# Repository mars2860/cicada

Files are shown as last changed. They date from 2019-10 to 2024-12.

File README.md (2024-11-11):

### About

The Cicada Project is the flight controller based on ESP8266 Wifi module. You can make it yourself to come in the world of drone developers. Cicada doesn't have a hardware pult with sticks. To control a drone there is desktop application developed on Java and mobile application for Android v7 and higher. You can connect a gamepad to your smartphone or desktop to control a drone. The flight controller can work in WiFi normal mode as WiFi station or WiFi Access Point. Also It can work in WiFi Broadcast mode (WiFi monitor mode). To work in broadcast mode you have to connect the special wifi broadcast serial modem to your smartphone or desktop. The serial modem is easy. You can do it yourself easy. Just ESP-07 module + UART-USB bridge. Flash in ESP-07 the modem firmware which is placed in the folder /firmware/WifiBroadcastModemFw.

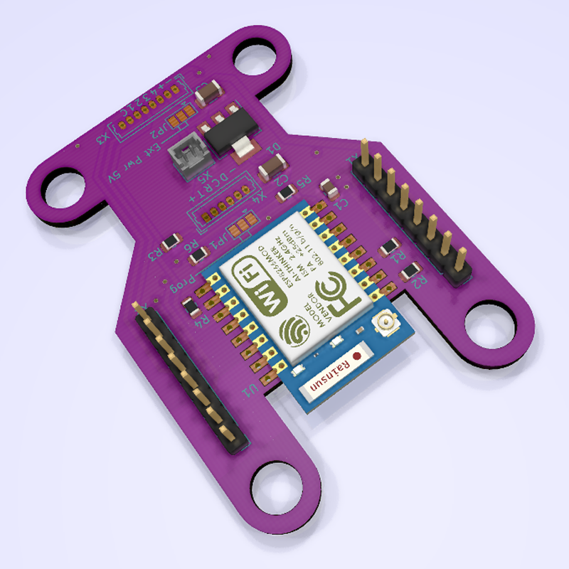
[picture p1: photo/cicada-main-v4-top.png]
cicada-main-v4

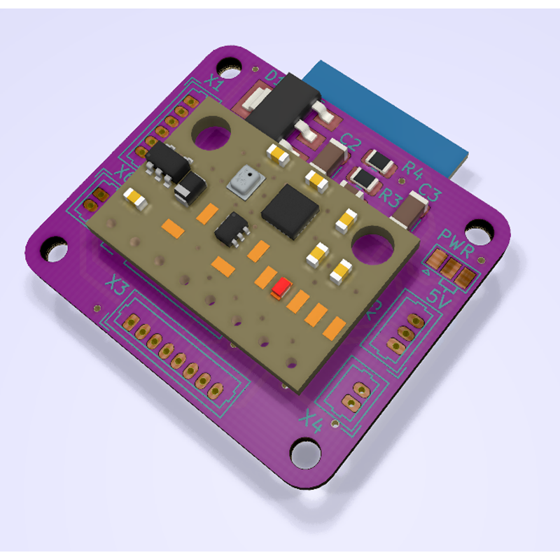
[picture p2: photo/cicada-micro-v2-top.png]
cicada-micro-v2

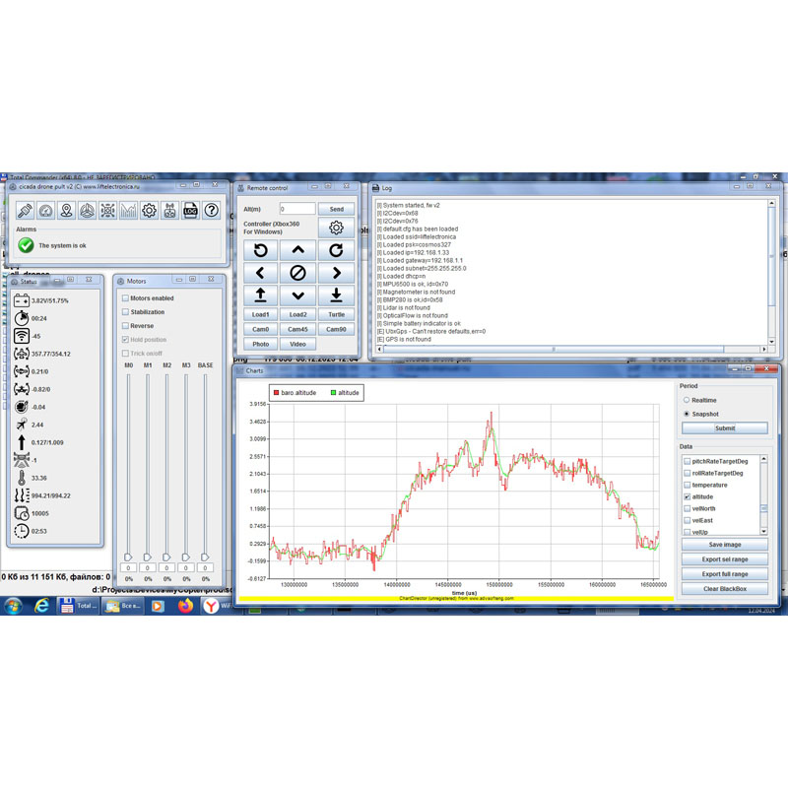
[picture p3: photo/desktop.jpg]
DesktopApp

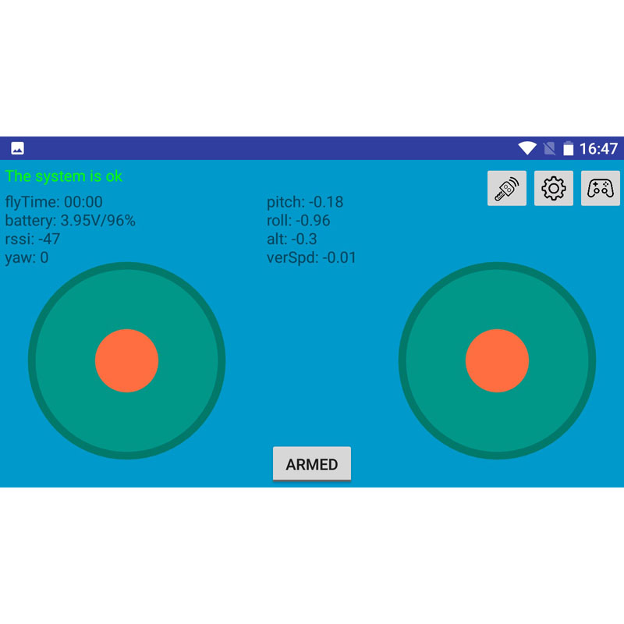
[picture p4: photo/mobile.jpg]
MobileApp


### Features

| | | | |
| --- | --- | --- | --- |
| | **Min** | **Typ** | **Max** |
| **1\. Supply voltage** | 3,4V | | 5V  |
| **2\. Update frequency** | | 100 Hz | |
| **3\. Control from notebook or smartphone through WiFi net.** | | 2.4 GHz | |
| **4\. Instant telemetry through WiFi net.** Charts of all parameters. BlackBox is stored on host. Telemetry packets is sent every 10ms. | | | |
| **5\. Control devices:**<br><br>* Gamepad (supported by desktop and mobile applications)<br>* Keyboard (supported by desktop application only)<br>* Virtual keyboard (supported by desktop application only)<br>* Virtual gamepad (supported by mobile application only) | | | |
| **6\. Control range** | | | 100 meters |
| **7\. Stabilization modes:**<br><br>* Stabilization of body angular rates<br>* Stabilization of yaw,pitch,roll angles<br>* Stabilization of vertical velocity (only if barometer or lidar are available in the system)<br>* Stabilization of horizontal velocity (only if optical flow sensor or GPS are available in the system) | | | |
| **8\. Supported sensors and devices:**<br><br>* MPU9250 - imu chip<br>* MPU6500 - imu chip<br>* MPU6050 - imu chip<br>* QMC5883L - magnetometer<br>* BMP280 - barometer<br>* VL53L1X - lidar<br>* TFmini Plus (in I2C mode) - lidar<br>* HCSR04 (in I2C mode) - sonar<br>* BN180 and other GPS modules with UBX protocol<br>* Analog 0-3V sensor of battery current<br>* Servo 500-2400us to control camera pitch angle<br>* Camera Runcam Split4 (only supported start/stop video commands) | | | |
| **9\. Electronic speed controllers:**<br><br>* DSHOT-300 to control BLDC motors<br>* All listed below PWM-modesе to direct control coreless dc motors<br>* PWM 2.5 kHz, resolution 2000<br>* PWM 5 kHz, resolution 1000<br>* PWM 10 kHz, resolution 500<br>* PWM 20 kHz, resolution 250<br>* PWM 40 kHz, resolution 125<br>* PWM 50 kHz, resolution 100 | | | |
| **10\. Dimensions**<br><br>* cicada-main-v4<br>* cicada-micro-v2 | | 58,67mm х 41,65mm  <br>26,67mm x 30,98mm | |
| **11\. Installation dimensions**<br><br>* cicada-main-v4<br>* cicada-micro-v2 | | 48,51mm х 31,49mm  <br>21,84mm x 26,16mm | |
| **12\. Weight**<br><br>* cicada-main-v4 with cicada-gy91-v3<br>* cicada-micro-v2 | | 16g  <br>6g | |
	
### Drones

Examples of drones you can find in drones folder of this project.

### Firmware

The firmware is based on PDL. Portable Drone Logic (PDL) is the lightweight pure C library implements a common drone logic. The goal of PDL is to be easy to use and easy to port to your hardware platform. PDL supports only quadcopters at this time.

It provides for you
- data model
- application template
- task scheduler
- chain of PIDs
- parser for binary digital commands

PDL is a part of this project. But you can use it to create firmware for your own hardware platform. Documentation is available in /firmware/CicadaFw/libraries/pdl

To build firmware you need
- Install Sloeber IDE https://github.com/Sloeber/arduino-eclipse-plugin/releases/
- Run Sloeber IDE. Go to Arduino->Preferences->Platforms and Boards. Download latest version of ESP8266 platform
- Install I2C driver https://github.com/enjoyneering/ESP8266-I2C-Driver
- Create ssid_config.h file with your wifi-net settings. For example

Firmware supports update by the air. It is based on ESP8266HTTPUpdateServer.

### Chain of PIDs

Chain of PIDs

### Design tools

- Sloeber IDE
- FreeCAD
- KiCAD

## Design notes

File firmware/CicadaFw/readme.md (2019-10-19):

### How to build

1. Install Sloeber IDE https://github.com/Sloeber/arduino-eclipse-plugin/releases/
2. Run Sloeber IDE. Go to Arduino->Preferences->Platforms and Boards. Download latest version of ESP8266 platform
3. Install I2C driver https://github.com/enjoyneering/ESP8266-I2C-Driver

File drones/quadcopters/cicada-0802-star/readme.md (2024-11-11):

# Cicada-0802

Cicada-0802-star is FPV quadcopter based on Cicada Flight Controller. Distance between motors 75mm in diagonal. Mass is 48 gram with GNB-380mAh-LiHv-1S. Time of flight is about 2 minutes.

# Parts List
- cicada-micro-v2 - flight controller based on ESP-12E module
- teeny pro 5a - electronic speed controller
- happymodel RS0802 KV20000 - motors
- HQProp 40MMX3GR  - propellers
- akk ba3 - camera

# Electrical schematic
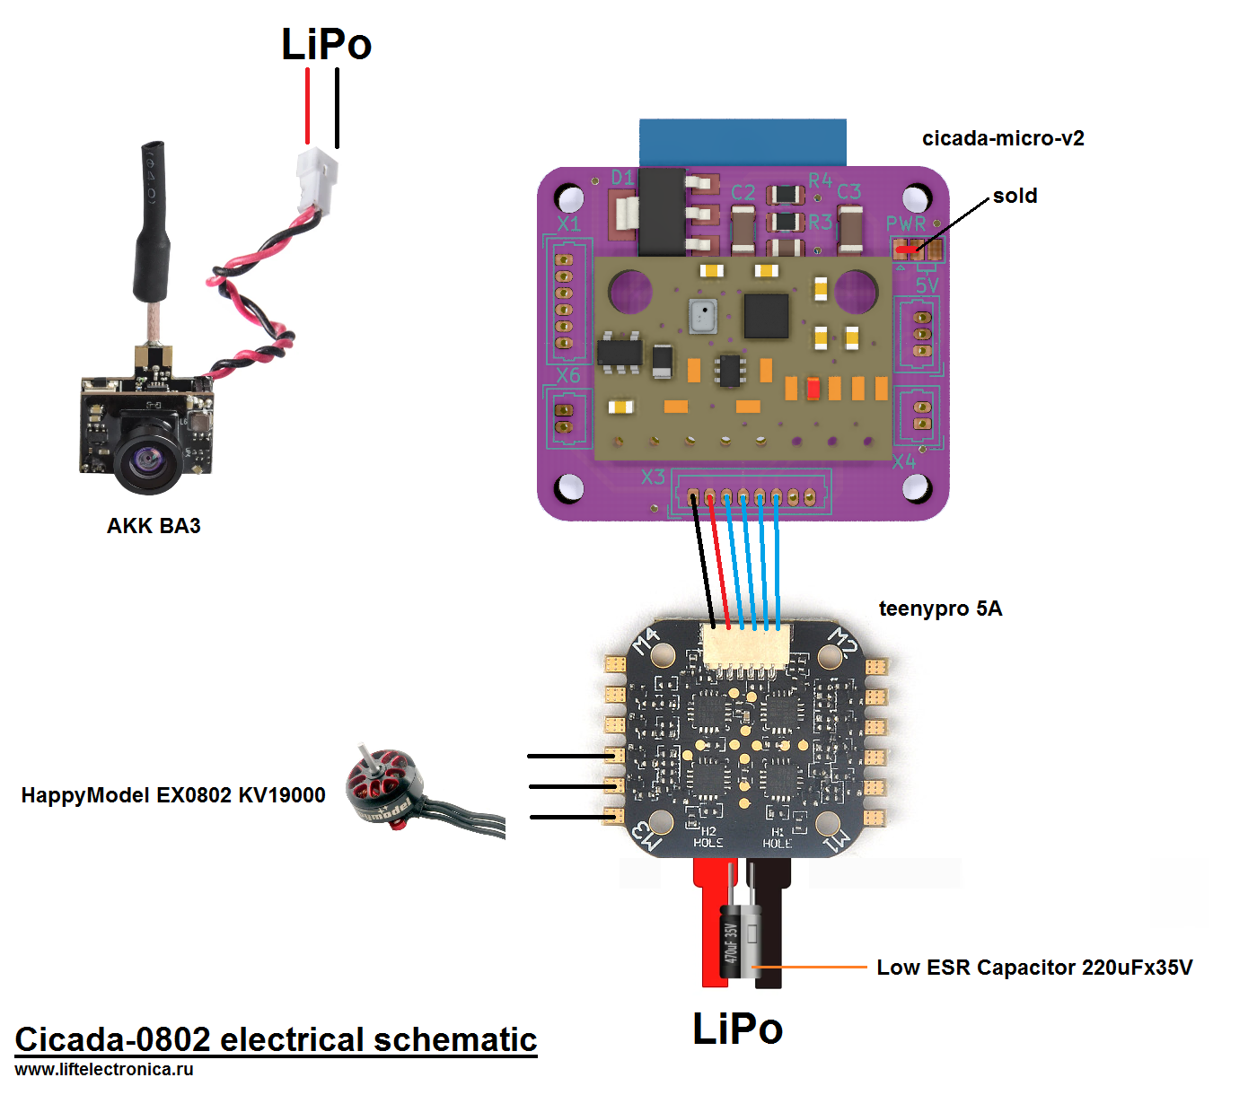
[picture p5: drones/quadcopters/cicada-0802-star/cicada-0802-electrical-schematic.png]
electrical schematic


# Views
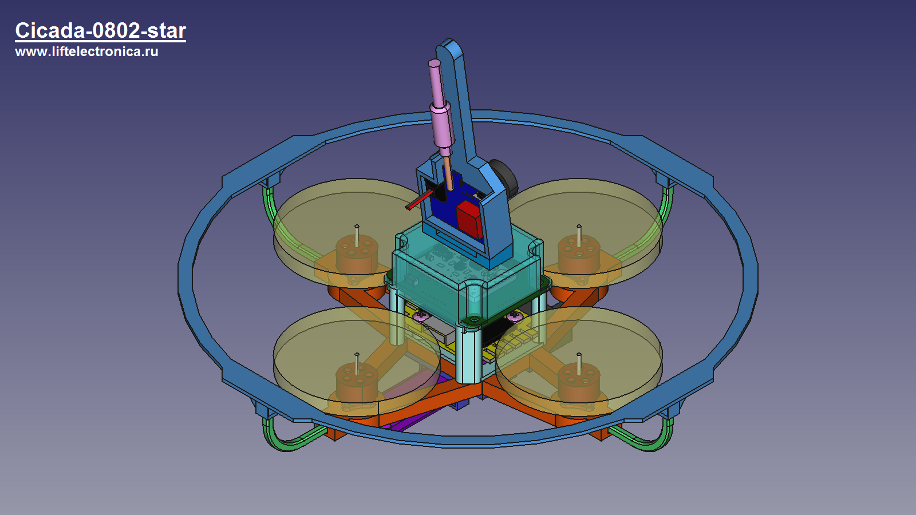
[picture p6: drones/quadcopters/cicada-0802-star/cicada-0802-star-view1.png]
view1

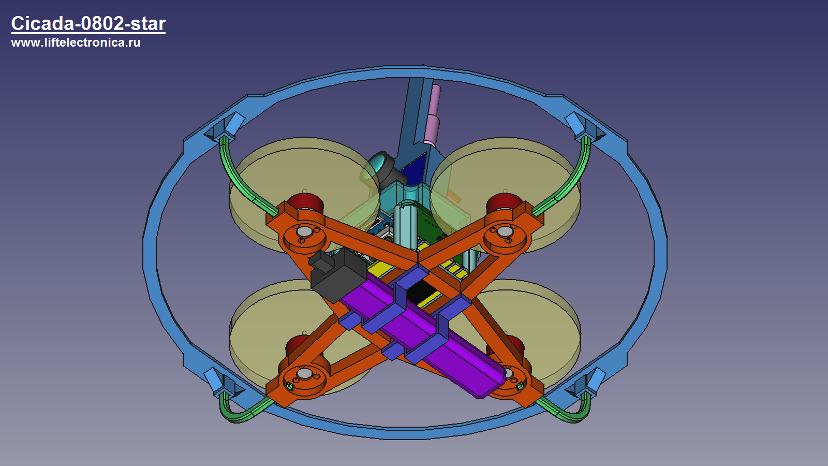
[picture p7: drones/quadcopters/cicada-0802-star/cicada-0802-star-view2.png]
view2


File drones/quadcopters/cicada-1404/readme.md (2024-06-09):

# Cicada-1404

Cicada-1404 is FPV quadcopter based on Cicada Flight Controller. Distance between motors 170mm in diagonal. Mass is 225 gram without gps module and propeller protection. As optional it can be equipped with GPS module. Time of flight is about 6 minutes with GNB-850mAh-80C-2S battery

# Parts List
- cicada-micro-v2 - flight controller based on ESP-07 module
  -- ESP-07 - wifi module (https://aliexpress.ru/item/32226333667.html)
  -- GY-91 module (https://aliexpress.ru/item/1005004770424192.html)
  -- LDL1117S33SR (https://www.chipdip.ru/product/ldl1117s33r-stm)
  -- Resistors 0805 3k3 6pieces (https://www.chipdip.ru/product0/8001961333)
  -- Resistor 0805 390k 1pieces (https://www.chipdip.ru/product0/8002001295)
  -- Resistor 0805 30k 1pieces (https://www.chipdip.ru/product0/8001968464)
  -- Capacitor 0805 100nF 1pieces (https://www.chipdip.ru/product/grm21br71h104k)
  -- Capacitor 1206 22uF 2pieces (https://www.chipdip.ru/product0/9001437124)
- skystars ko25 - electronic speed controller (https://aliexpress.ru/item/1005003703593525.html)
- skystars koko 1404 KV4600 - motors (https://aliexpress.ru/item/1005002967385400.html)
- HQProp T3x2x2 - propellers (https://aliexpress.ru/item/4000082192022.html)
- runcam split4 - camera (https://aliexpress.ru/item/4001286069840.html)
- akk fx3 - 5.8 GHz video transmitter (https://aliexpress.ru/item/32886948514.html)
- antenna 5.8 GHz with MMCX connector (https://aliexpress.ru/item/4000109363746.html)
- SG-90 - servo to control camera pitch (https://aliexpress.ru/item/1005006027280940.html)
- IFlight M8Q-5883 - GPS module (optional) (https://aliexpress.ru/item/1005006376325669.html)
- gnb-850-80C-2S - battery (https://aliexpress.ru/item/1005005952282974)
- mp1584en - dc-dc step down power module (https://aliexpress.ru/item/1005001621925314.html)

# Electrical schematic
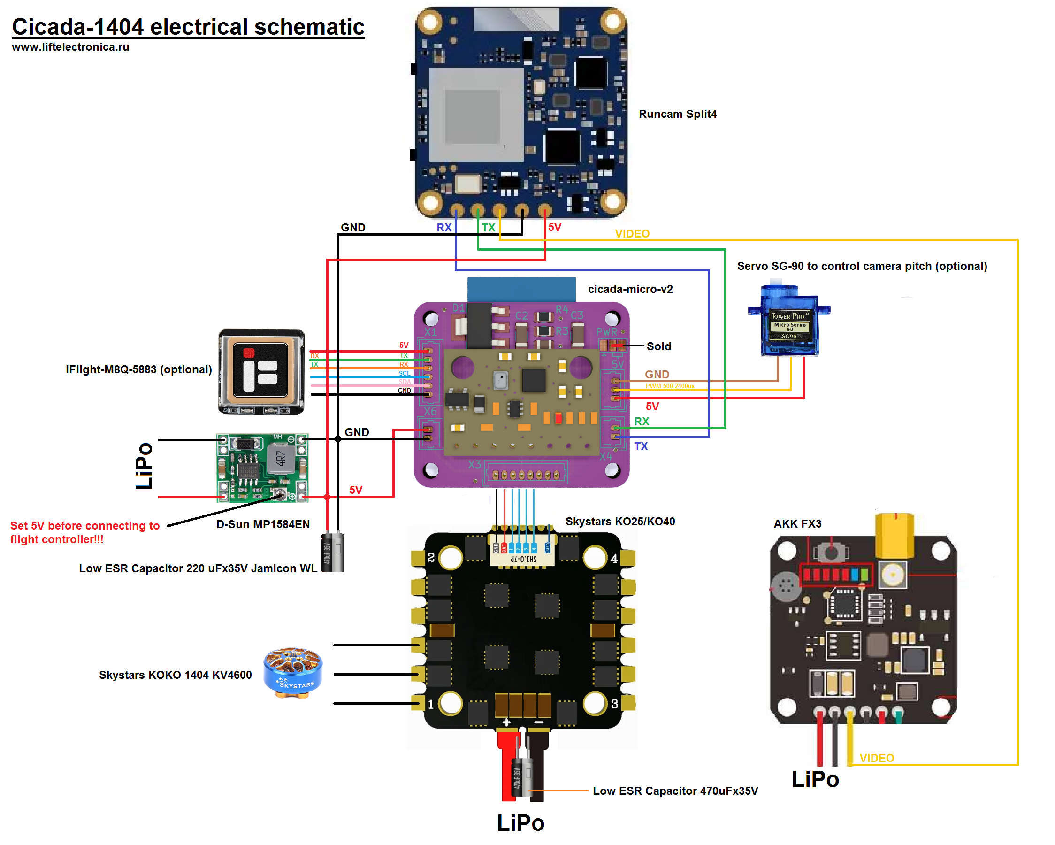
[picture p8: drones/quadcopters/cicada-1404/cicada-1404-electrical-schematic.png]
electrical schematic


# Views
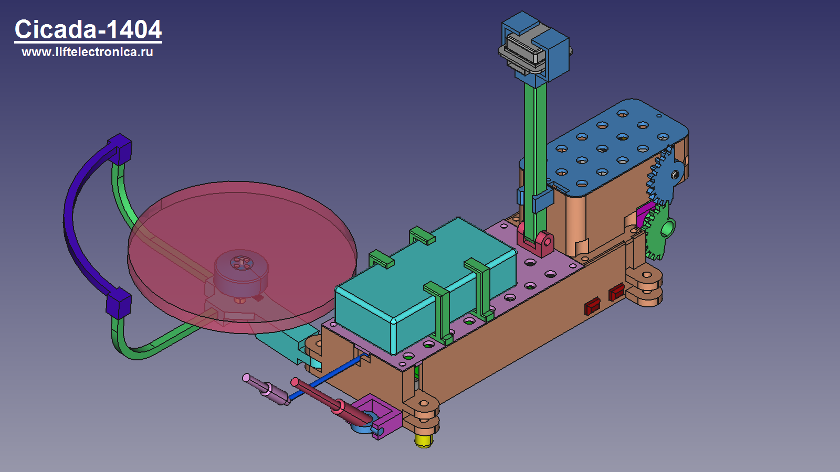
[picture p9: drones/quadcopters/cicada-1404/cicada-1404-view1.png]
view1

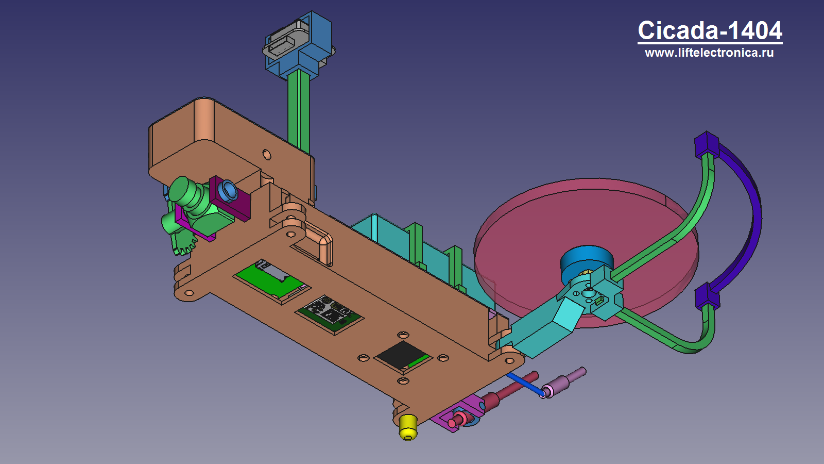
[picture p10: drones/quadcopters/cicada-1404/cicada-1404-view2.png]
view2


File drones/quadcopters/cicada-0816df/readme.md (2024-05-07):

# Cicada-0816df

Cicada-0816df is FPV quadcopter based on Cicada Flight Controller. Distance between motors 96mm in diagonal. Mass is 94 gram. Time of flight is about 2 minutes with GNB-550mAh-90C-1S battery. Ducted fans were made based on [this article](https://capolight.wordpress.com/2015/01/14/quadcopter-rotor-duct/) Its really increase thrust of propellers but this increasing is eaten by weight of ducts. Also ducted fans increase stabilization by pitch/roll but strongly decrease stabilization by yaw.

# Parts List
- cicada-micro-v2 - flight controller based on ESP-12E module
- cicada-pwm-esc-v3 - electronic speed controller
- coreless dc 816 motors
- HQProp 41mm-3blades or Gemfan 1636 - propellers
- ewrf7082ve - camera

# Electrical schematic
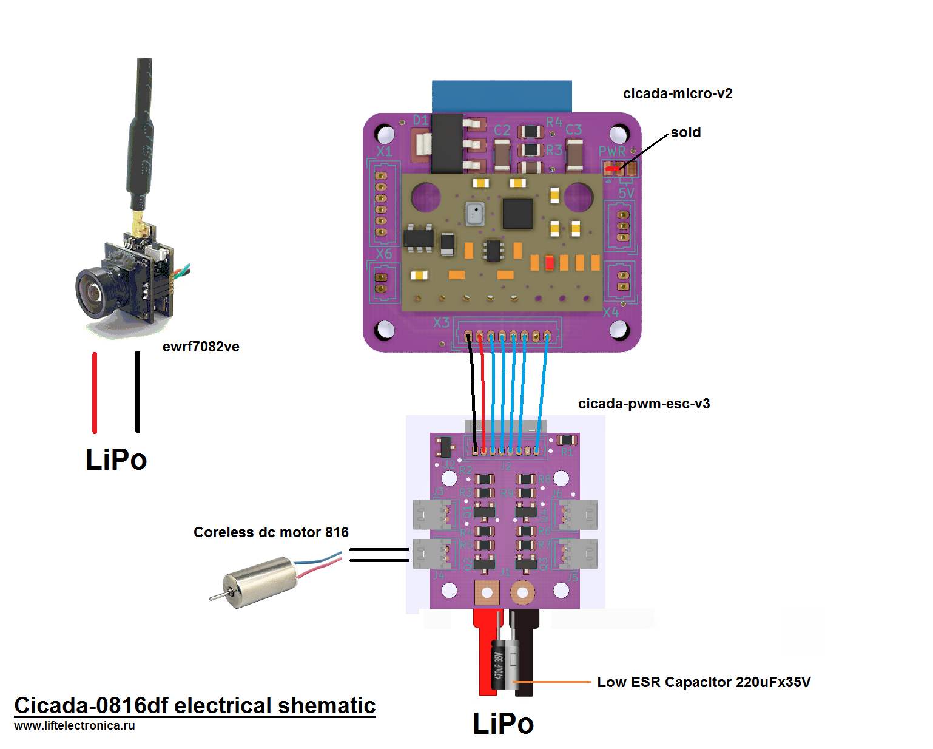
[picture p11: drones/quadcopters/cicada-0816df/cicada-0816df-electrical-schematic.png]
electrical schematic


# Views
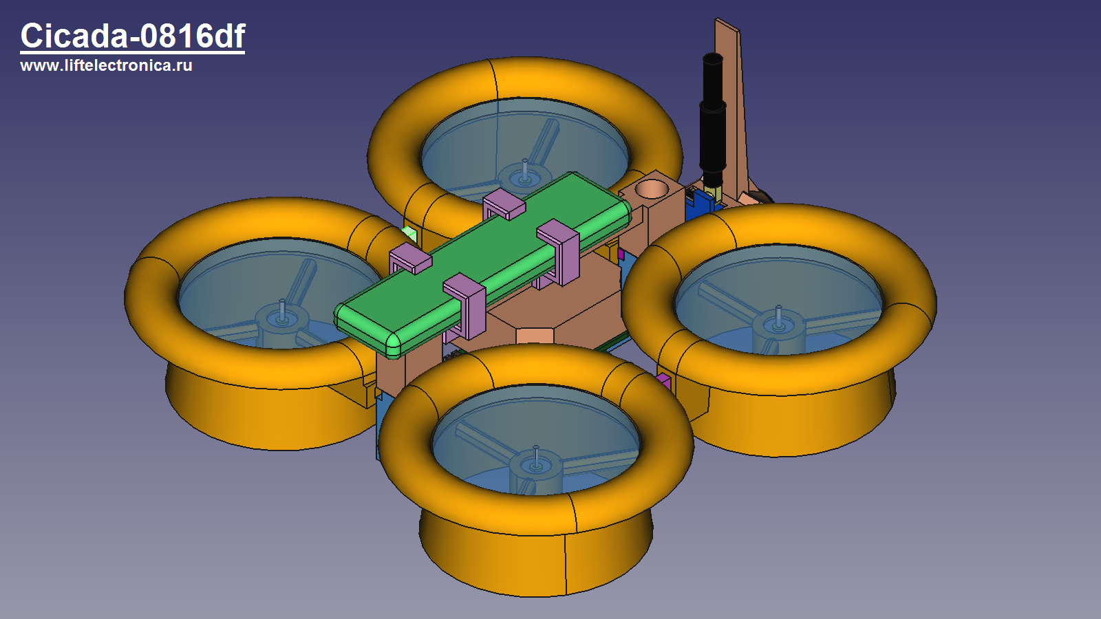
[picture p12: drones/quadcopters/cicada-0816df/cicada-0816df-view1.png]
view1

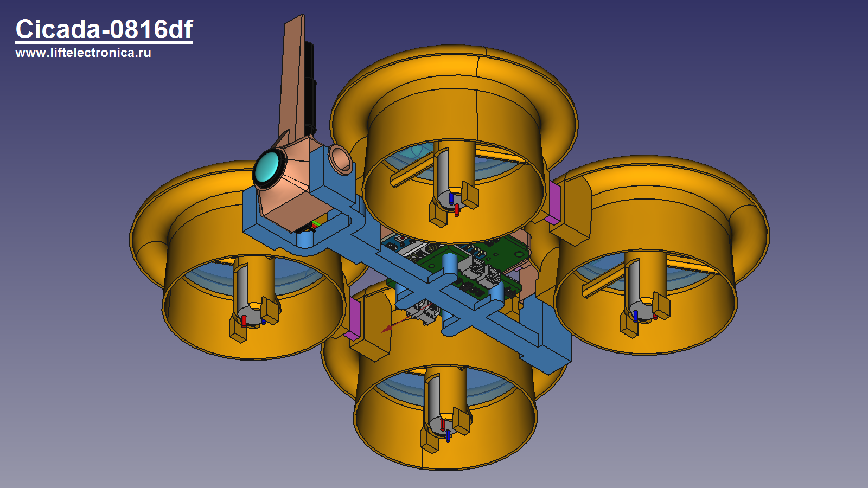
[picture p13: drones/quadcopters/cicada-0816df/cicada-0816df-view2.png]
view2


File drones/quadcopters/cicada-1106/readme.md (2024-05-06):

# Cicada-1106

Cicada-1106 is FPV quadcopter based on Cicada Flight Controller. Distance between motors 220mm in diagonal. Mass is 235 gram without propeller protection. Time of flight is about 5 minutes with GNB-850mAh-80C-2S battery

# Parts List
- cicada-main-v4 - flight controller based on ESP-07 module
- cicada-gy91-v3 - expansion board
- skystars ko25 - electronic speed controller
- aliexpress 1106 KV4200 - motors
- aliexpress 4045 - propellers
- ewrf7082ve - camera
- BN-180 - GPS module
- TFmini Plus - lidar
- CJMCU-PMW3901 - optical flow sensor

# Electrical schematic
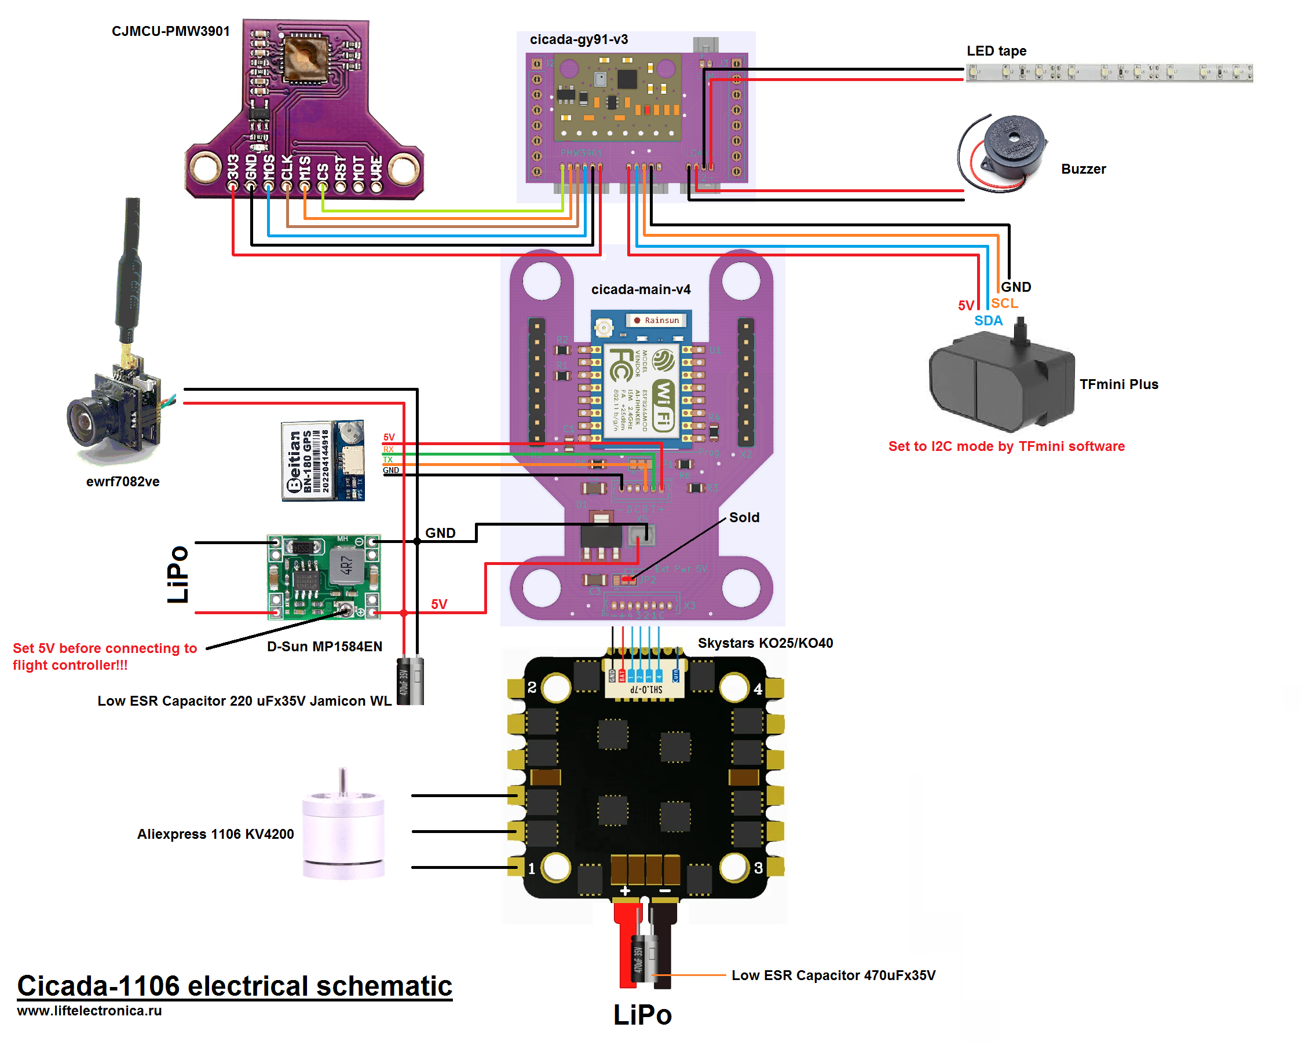
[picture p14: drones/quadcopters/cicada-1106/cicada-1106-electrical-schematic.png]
electrical schematic


# Views
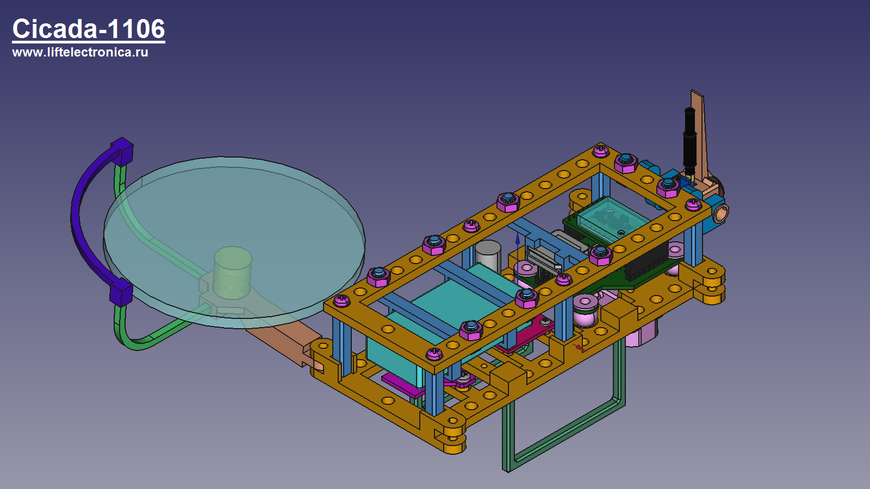
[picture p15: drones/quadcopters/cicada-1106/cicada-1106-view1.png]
view1

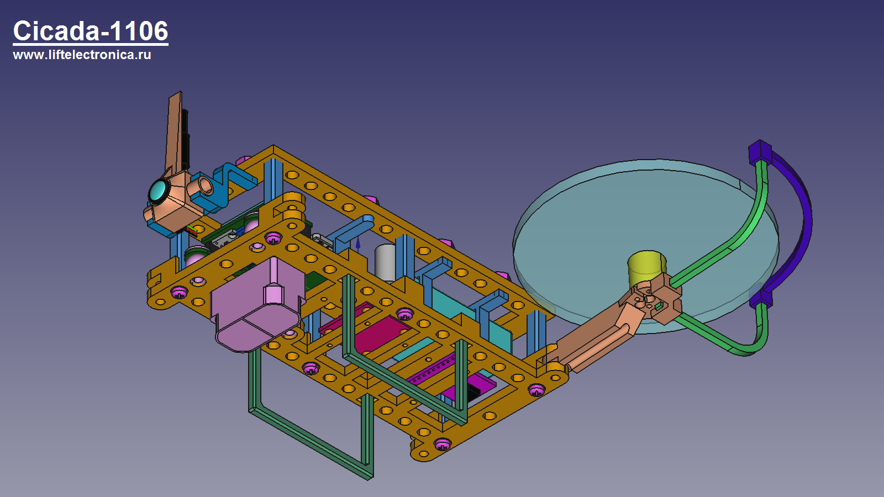
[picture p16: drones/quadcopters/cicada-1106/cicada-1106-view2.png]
view2


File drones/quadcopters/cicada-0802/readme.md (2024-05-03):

# Cicada-0802

Cicada-0802 is FPV quadcopter based on Cicada Flight Controller. Distance between motors 82mm in diagonal. Mass is 59 gram. Time of flight is about 3 minutes with GNB-550mAh-90C-1S battery.

# Parts List
- cicada-micro-v2 - flight controller based on ESP-12E module
- teeny pro 5a - electronic speed controller
- happymodel 0703 or 0802 KV19000 - motors
- HQProp 41mm-3blades or Gemfan 1609 - propellers
- akk ba3 or ewrf7082ve - camera

# Electrical schematic
electrical schematic

# Views
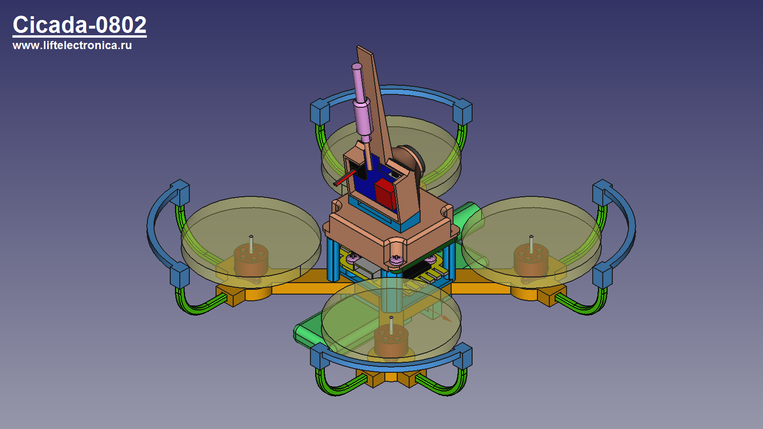
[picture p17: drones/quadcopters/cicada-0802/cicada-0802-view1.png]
view1

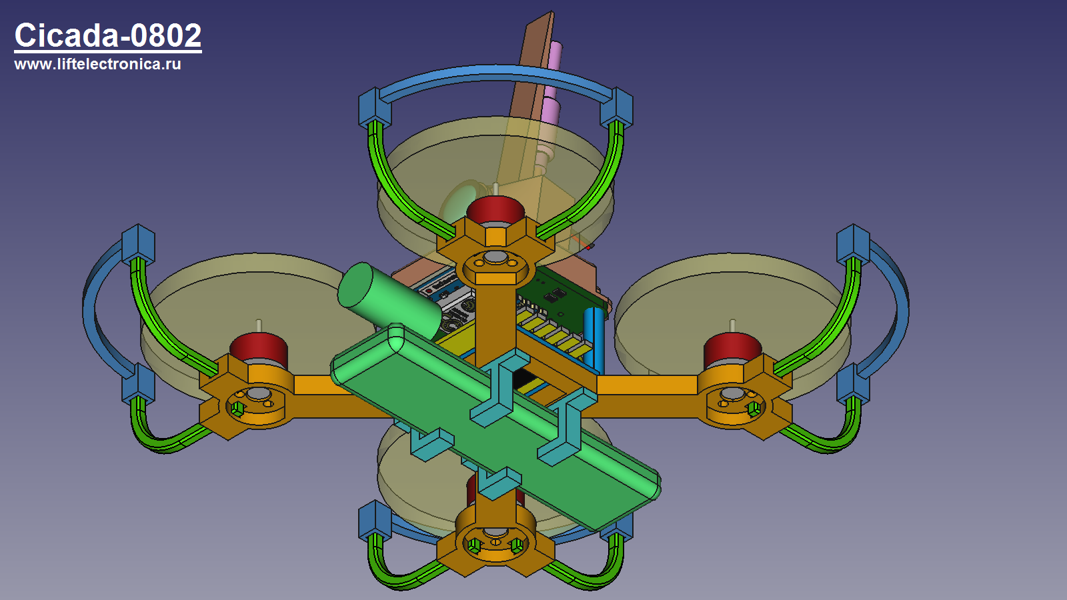
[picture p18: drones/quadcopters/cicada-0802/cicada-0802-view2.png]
view2


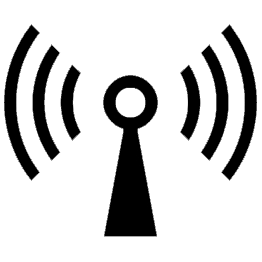
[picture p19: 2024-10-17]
software/desktop/CicadaDronePult/src/main/images/radio.png

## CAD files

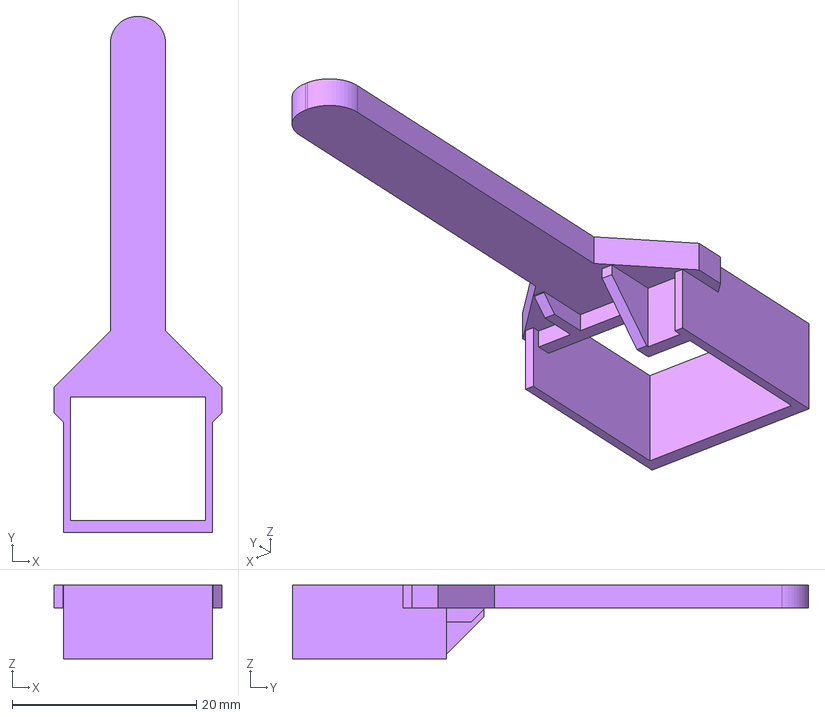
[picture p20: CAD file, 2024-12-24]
drones/common-parts/case-for-eachine-tx06.FCStd
18.2 x 56.0 x 8.00 mm

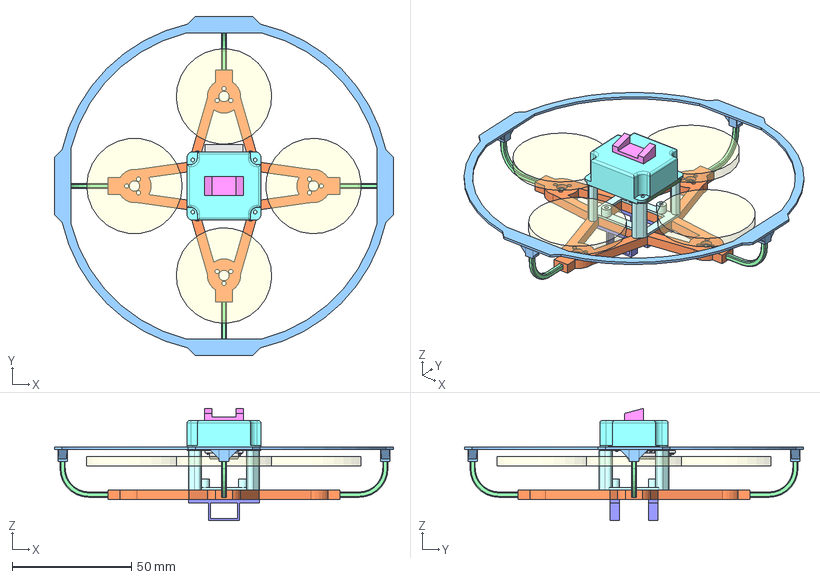
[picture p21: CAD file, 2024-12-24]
drones/quadcopters/cicada-0802-star/cicada-0802-star.FCStd
142.0 x 142.0 x 47.0 mm
bat-gnb-lihv-380-holder-001
bat-gnb-lihv-380-holder-002
cam-tx06-sub-plate-deg15
HQProp-40mm-3blades-002 x 4
race-star-frame
prot-leg-with-key-001
prot-leg-with-key-002
prot-leg-with-key-003
prot-leg-with-key-004
pcb-holder-h16.5
protection-big-ring-v3
imu-cup-mpu6050-and-bmp280-v2

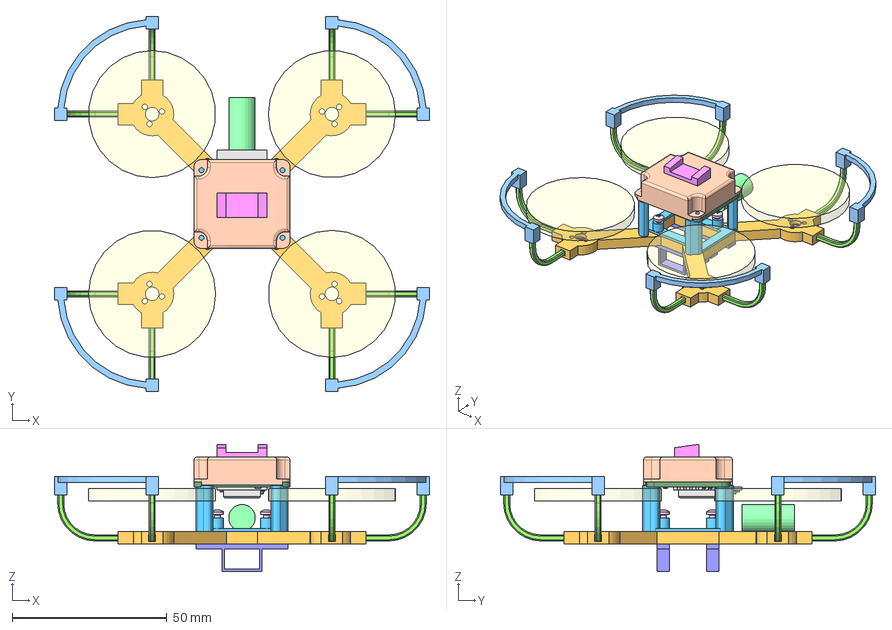
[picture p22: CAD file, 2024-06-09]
drones/quadcopters/cicada-0802/cicada-0802.FCStd
121.0 x 121.0 x 41.1 mm
HQProp-41mm-3blades x 4
prot-ring x 4
prot-leg-01 x 4
prot-leg-02 x 4
imu-cup-gy91
M2x5-Screw
M2x5-Screw016
M2x5-Screw014
M2x5-Screw015
capacitor
pcb-holder
3d-printed-frame
bat-gnb-lihv-380-holder-001
bat-gnb-lihv-380-holder-002
cam-tx06-sub-plate

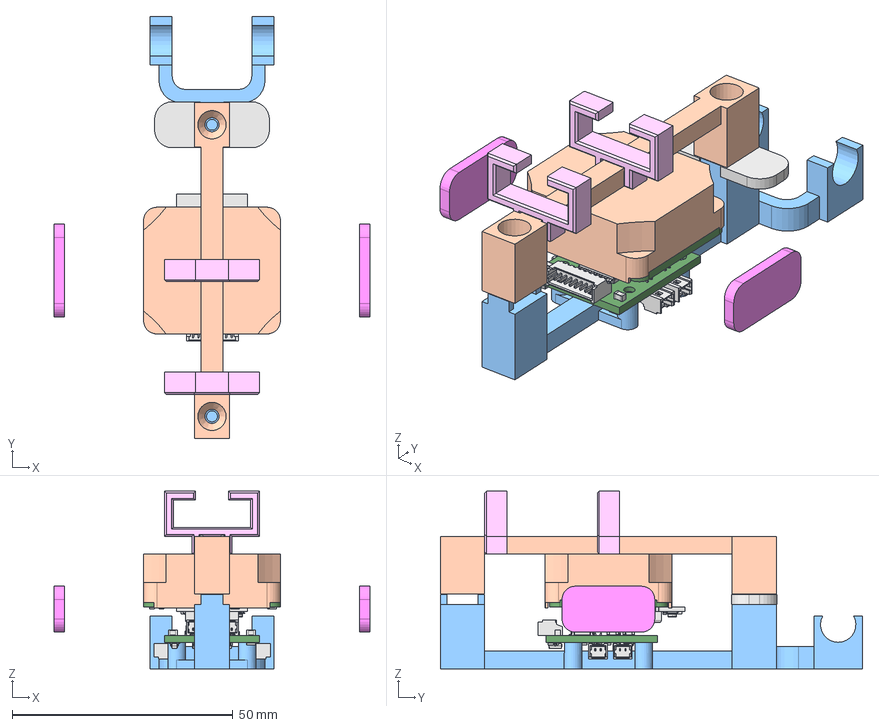
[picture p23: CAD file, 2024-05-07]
drones/quadcopters/cicada-0816df/cicada-0816df.FCStd
71.4 x 95.5 x 40.2 mm
bat-gnb-1s-holder-v2-001 x 2
btw-shroud-wall-001 x 2
top
bottom
shroud-holder-v2

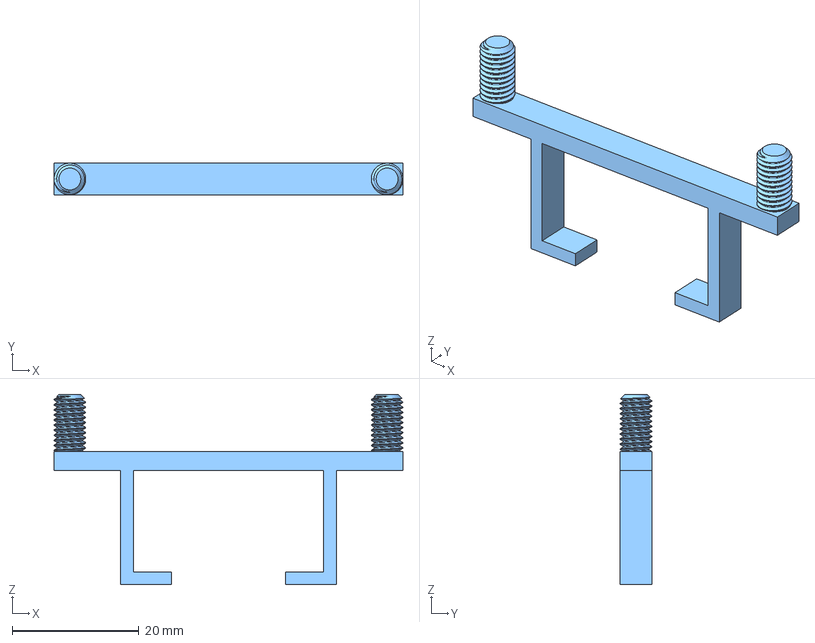
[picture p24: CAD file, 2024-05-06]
drones/quadcopters/cicada-1106/bat-gnb-850-2s-holder.FCStd
55.0 x 5.00 x 30.0 mm

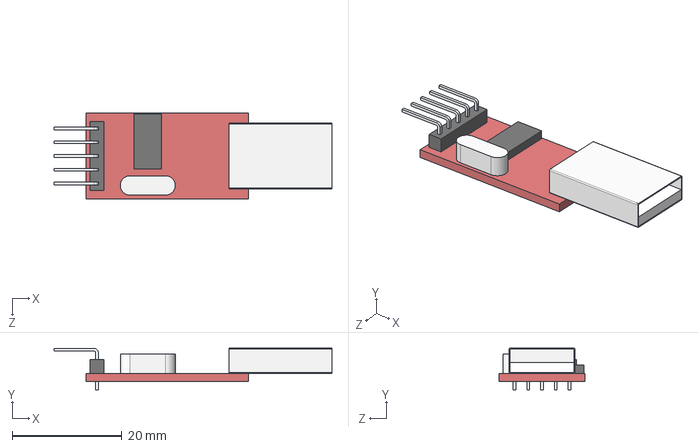
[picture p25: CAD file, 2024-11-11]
drones/third-party-parts/converter-usb-uart.step
50.5 x 7.60 x 15.6 mm

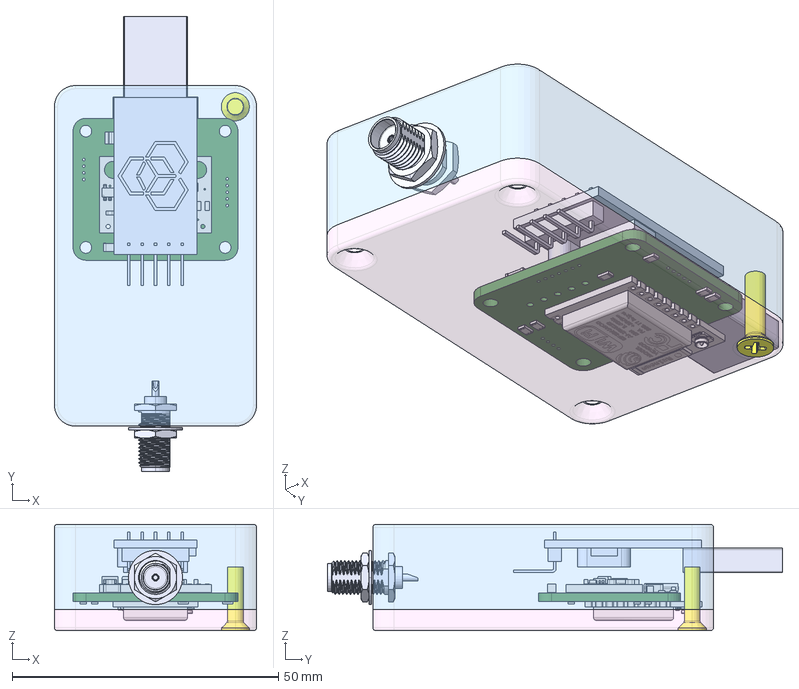
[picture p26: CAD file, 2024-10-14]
drones/wifi-broadcast-modem/wifi-broadcast-modem.FCStd
38.0 x 85.5 x 20.0 mm
USB - UART
RP-SMA
M3x12-Screw
Lid-2
Lid-1

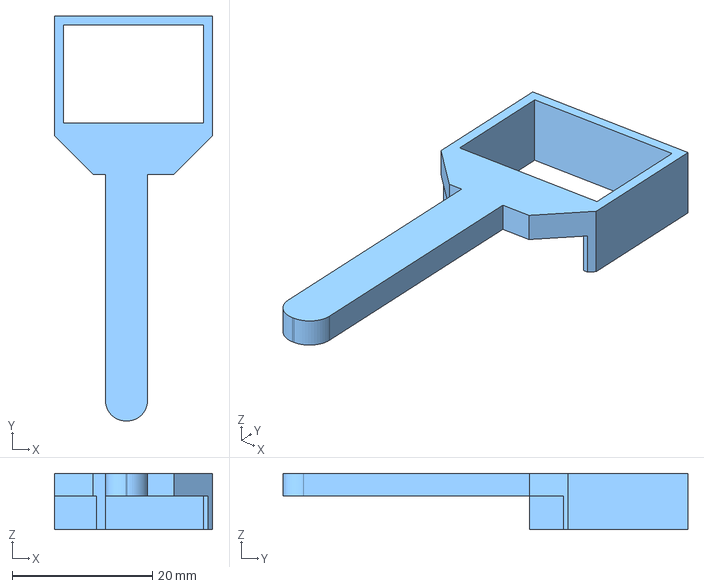
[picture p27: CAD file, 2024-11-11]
drones/common-parts/case-for-akk-ba3-strong.FCStd
22.6 x 57.8 x 8.00 mm

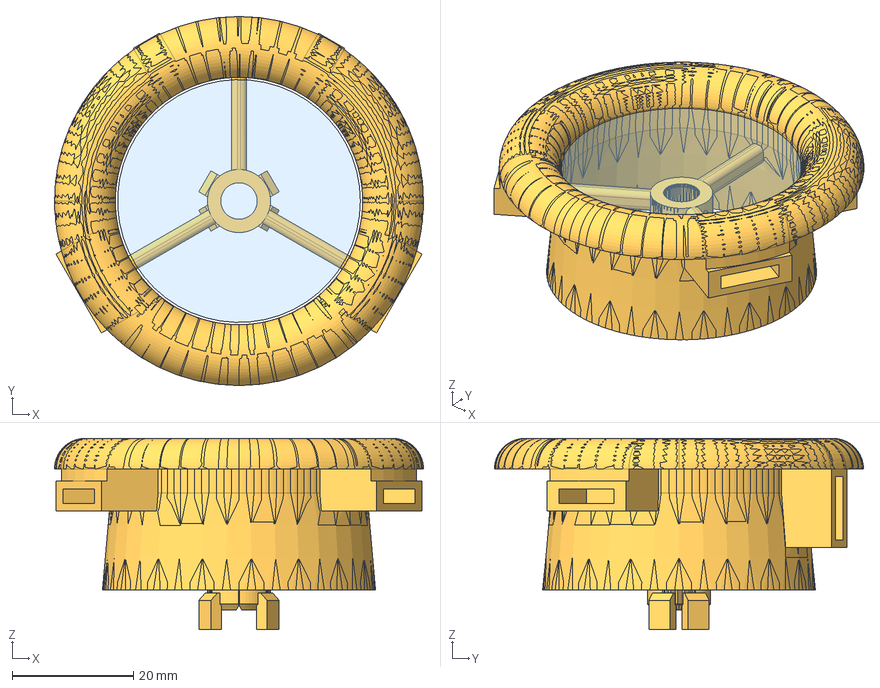
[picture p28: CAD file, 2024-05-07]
drones/quadcopters/cicada-0816df/prop-d40-shroud-0816.FCStd
60.8 x 60.8 x 31.5 mm
prop-d40 x 2
prop-d40-shroud-816-v2
prop-d40-shroud-816-v003 (Mirror #1)

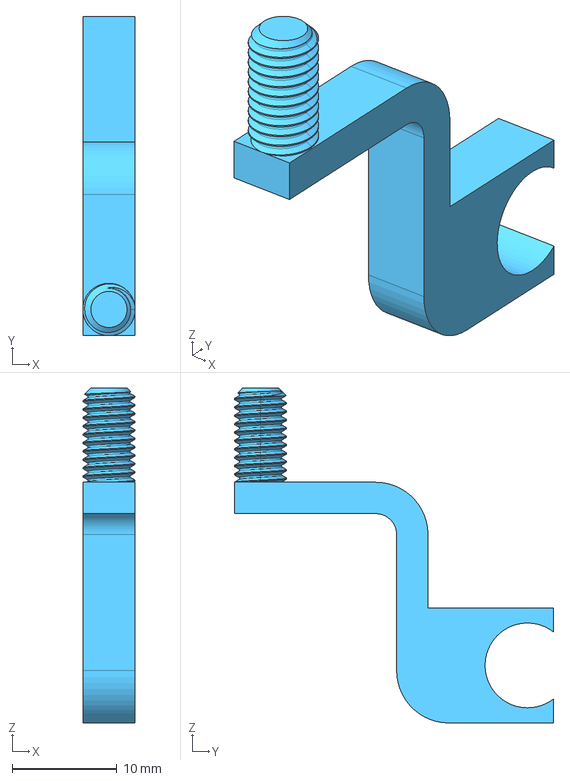
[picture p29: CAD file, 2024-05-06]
drones/quadcopters/cicada-1106/cam-ewrf7082ve-holder.FCStd
5.00 x 30.5 x 32.0 mm

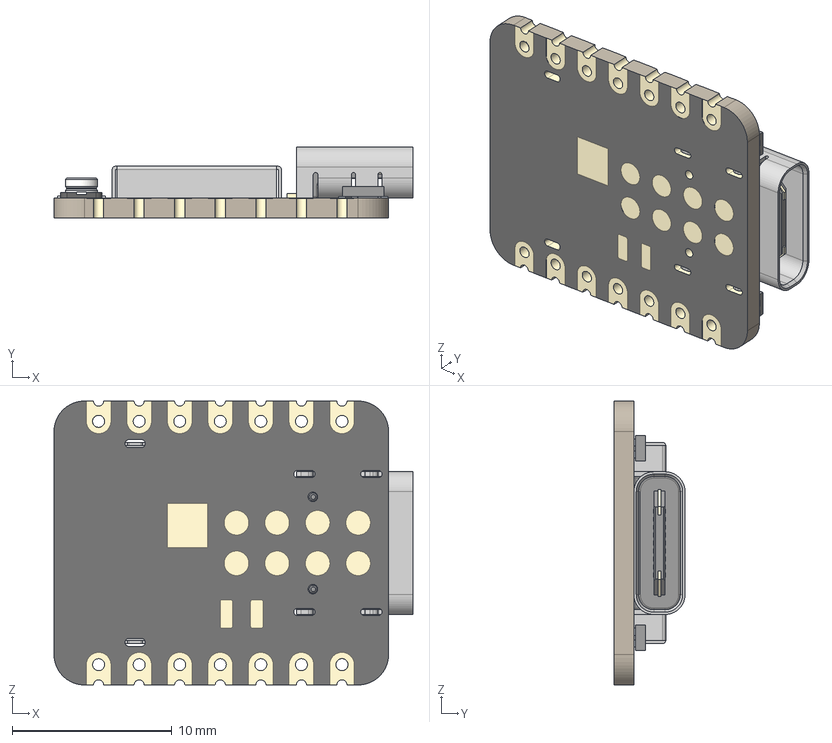
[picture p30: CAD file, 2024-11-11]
drones/third-party-parts/xiao-esp32-s3-v3.step
22.5 x 4.46 x 17.8 mm
BOSS-EXTRUDE14_8_
BOSS-EXTRUDE7_4_
BOSS-EXTRUDE7_3_
BOSS-EXTRUDE14_4_
BOSS-EXTRUDE14_2_
BOSS-EXTRUDE14_11_
BOSS-EXTRUDE7_7_
BOSS-EXTRUDE14_9_
BOSS-EXTRUDE14_3_
BOSS-EXTRUDE14_7_
MIRROR2
BOSS-EXTRUDE14_5_
BOSS-EXTRUDE14_12_
BOSS-EXTRUDE7_8_
BOSS-EXTRUDE7_1_
BOSS-EXTRUDE14_10_
BOSS-EXTRUDE7_9_
BOSS-EXTRUDE14_6_
BOSS-EXTRUDE14_1_
BOSS-EXTRUDE7_6_
BOSS-EXTRUDE7_2_
CUT-EXTRUDE5
BOSS-EXTRUDE7_5_
Shield
Pins x 2
U.FL-R-SMT-1_10_ v1

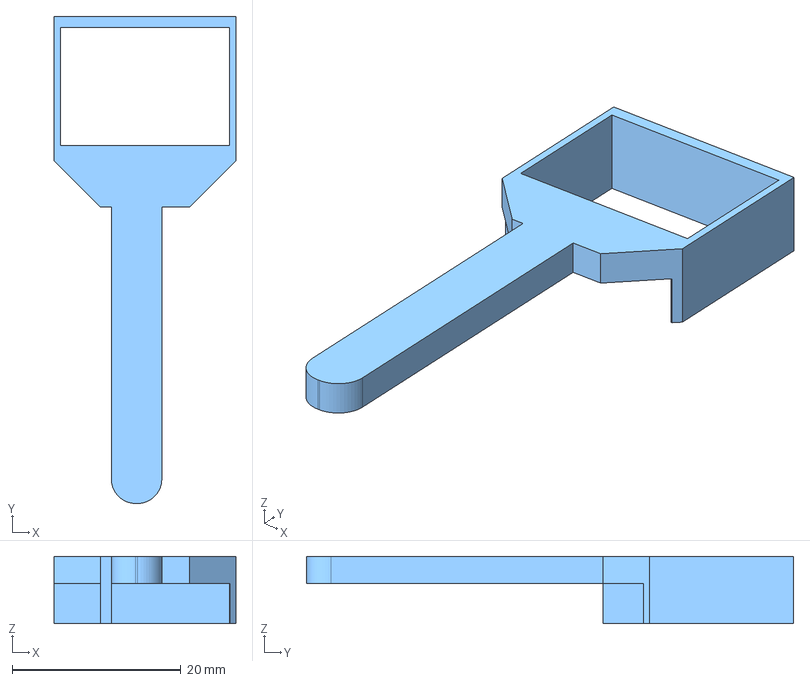
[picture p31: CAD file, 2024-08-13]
drones/common-parts/case-for-akk-ba3-light.FCStd
21.6 x 57.8 x 8.00 mm

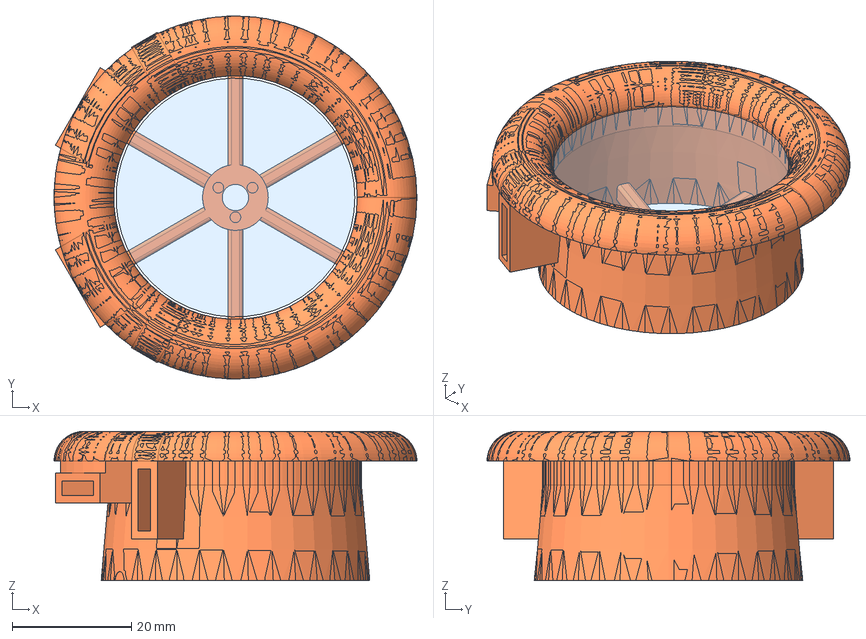
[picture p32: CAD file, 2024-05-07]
drones/quadcopters/cicada-0816df/prop-d40-shroud-0703.FCStd
60.8 x 60.8 x 25.0 mm
prop-d40 x 2
prop-d40-shroud-v4
prop-d40-shroud-v005 (Mirror #1)

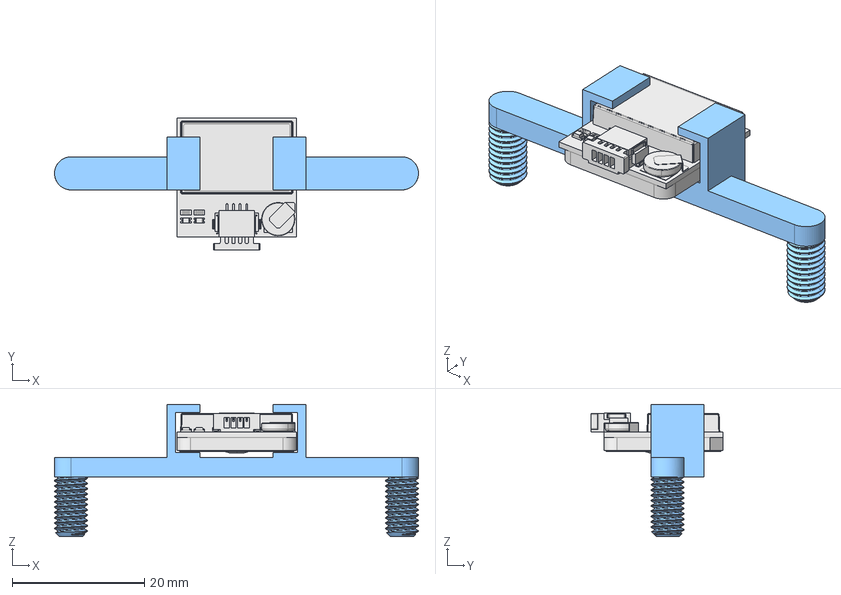
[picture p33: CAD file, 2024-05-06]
drones/quadcopters/cicada-1106/bn-180-holder.FCStd
55.0 x 20.0 x 20.0 mm
bn-180-holder-v3

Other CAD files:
drones/third-party-parts/esc-xeon-xr4a.FCStd
drones/common-parts/prop-d102-protection.FCStd
drones/third-party-parts/connector-jst-12p.step
drones/common-parts/motor-816-holder.FCStd
drones/common-parts/antenna-holder-2G4Hz-3dbi.FCStd
drones/common-parts/case-for-akk-ba3.FCStd
drones/common-parts/case-for-ewrf7082ve.FCStd
drones/common-parts/prop-d102-1106-ray.FCStd
drones/common-parts/prop-d80-ray.FCStd
drones/third-party-parts/antenna-2G4Hz-3dbi.FCStd
drones/third-party-parts/antenna-5G8Hz-3dbi.FCStd
drones/third-party-parts/bat-gnb-550-90c-1s.FCStd
drones/third-party-parts/bat-gnb-850-80c-2s.FCStd
drones/third-party-parts/bat-gnb-lihv-380-60c-1s.FCStd
drones/third-party-parts/camera-akk-ba3.FCStd
drones/third-party-parts/camera-eachine-tx06.FCStd
drones/third-party-parts/camera-ewrf7082ve.FCStd
drones/third-party-parts/connector-rp-sma.step
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

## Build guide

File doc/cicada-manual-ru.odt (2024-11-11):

Полётный контроллер квадрокоптера

Cicada

Руководство пользователя

версия документа 3

# Назначение и характеристики устройства

Полётный контроллер Cicada предназначен для управления квадрокоптерами. Отличительной особенностью данного полётного контроллера является канал управления и телеметрии по WiFi сети, что позволяет управлять квадрокоптером с ноутбука или смартфона. Для этого разработаны десктоп-приложение для Windows и мобильное приложение для Android.

Технические характеристики:

| Мин. | Рек./Ном. | Макс.
1. Напряжение питания | 3,4V | | 5V
2. Частота обновления | | 100 Гц
3. Управление с ноутбука или смартфона по WiFi сети | | 2,4 ГГц
4. Мгновенная телеметрия по WiFi сети. Графики всех параметров. Чёрный ящик сохраняется на хосте. Пакеты со всеми данными о состоянии системы и датчиков отправляются каждые 10мс.
5. Устройства управления: Геймпад (поддерживается как десктоп так и мобильным приложением) Клавиатура (только в десктоп-приложении) Виртуальная клавиатура (только в десктоп-приложении) Виртуальные джойстики (только в мобильном приложении)
6. Дальность управления | | | 100м
7. Режимы стабилизации: Акро - по угловым скоростям Горизонт - по крену, тангажу и курсу Вертикальная скорость - при наличии барометра или лидара Горизонтальная скорость - при наличии оптического датчика смещения или GPS
8. Поддерживаемые датчики и устройства: MPU9250 - imu модуль MPU6500 - imu модуль MPU6050 - imu модуль QMC5883L - магнетометр BMP280 - барометр VL53L1X - лидар TFmini Plus (в режиме I2C) - лидар HCSR04 (в режиме I2C) - сонар BN180 и другие модули GPS с протоколом UBX Аналоговый 0-3V датчик тока батареи Сервопривод с ШИМ управлением 500мкс — 2400мкс для управления углом наклона камеры Камера Runcam Split 4 (только включение и выключение записи видео)
9. Протоколы управления регулятором моторов: для бесколлекторных двигателей DSHOT-300 для прямого управления коллекторными двигателями ШИМ 2,5KHz 11 bit (2000 позиций) ШИМ 5KHz 10 bit (1000 позиций) ШИМ 10KHz 9bit (500 позиций) ШИМ 20KHz 8bit (250 позиций) ШИМ 40KHz 7bit (125 позиций) ШИМ 50KHz 6,6bit (100 позиций)
10. Габаритные размеры Модификация №1 - cicada-main-v4 Модификация №2 - cicada-micro-v2 | | 58,67мм х 41,65мм 26,67мм x 30,98мм
11. Установочные размеры Модификация №1 - cicada-main-v4 Модификация №2 - cicada-micro-v2 | | 48,51мм х 31,49мм 21,84мм x 26,16мм
12. Масса Модификация №1 - cicada-main-v4 Модификация №3 - cicada-micro-v2 | | 16г 6г

Разработаны 2 модификации данного полетного контроллера.

Модификация №1 — cicada-main.

Модификация №1 предназначена под установку на мягкие резиновые стойки (софтмаунт). Питание от Li-Po батареи в диапазоне напряжений 3.4V – 8.4V или внешнего dc-dc преобразователя на 5В. Содержит слоты для установки платы расширения. Данная модификация не может управлять квадрокоптером без платы расширения. Плата расширения — это дополнительная плата, на которой установлены гироскоп, акселерометр и дополнительные датчики в зависимости от типа платы расширения. Отличительной особенностью данной модификации является, то что она позволяет задействовать все возможные датчики, которые поддерживает программное обеспечение. Данную модификацию рекомендуется устанавливать на квадрокоптеры с размером рамы 200мм и более.

Модификация №2 — cicada-micro.

Модификация №2 предназначена для установки на микромодели. Эта модификация работает без платы расширения так как уже содержит модуль с гироскопом, акселерометром и барометром. Цель данной модификации — это минимальная масса.

# Окно настроек

Чтобы посмотреть или изменить настройки полётного контроллера необходимо открыть окно настроек в десктоп-приложении на ноутбуке или стационарном ПК. Для запуска десктоп-приложения необходимо установить среду исполнения Java программ JRE v7 или выше. После установки JRE зайдите в папку десктоп-приложения и выполните файл run.bat для запуска десктоп-приложения. Далее, чтобы посмотреть или изменить настройки, необходимо нажать на кнопку «Настройки».

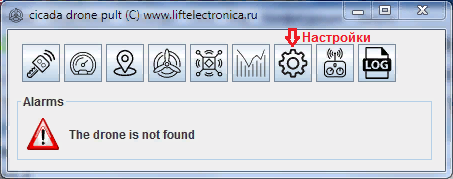
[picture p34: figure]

После этого откроется окно настроек.

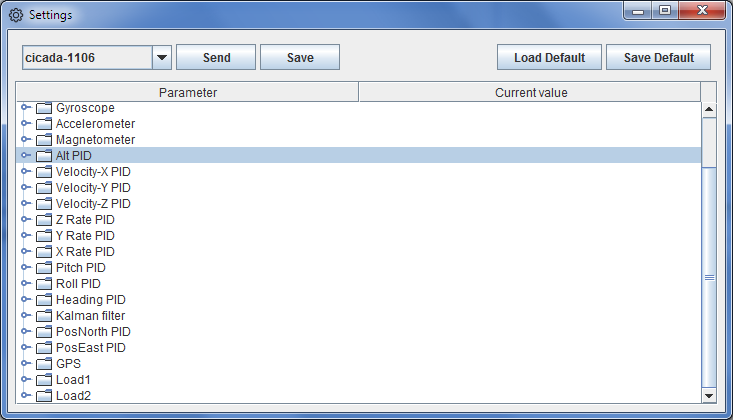
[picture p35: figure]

Внимание: Все настройки хранятся на диске вашего хоста (ноутбуке/смартфоне). Каждый раз, когда вы включаете ваш полётный контроллер и Нажимаете на кнопку «Подключить», то в этот момент настройки читаются из файла на диске вашего хоста и далее передаются по WiFi сети на ваш полётный контроллер. Сам полётный контроллер хранит настройки в своем ОЗУ и после выключения питания они пропадают. Поэтому если, например, вы настроили полётный контроллер на ноутбуке, а потом пытаетесь управлять им со смартфона, не скопировав настройки с ноутбука, то ваша модель разобьётся. В своей энергонезависимой памяти полётный контроллер сохраняет только настройки подключения к сети WiFi и настройки по умолчанию.

Если, например, вы настроили полётный контроллер на ноутбуке и хотите скопировать настройки на смартфон, то можете сохранить текущие настройки как настройки по умолчанию на флеш-память полётного контроллера. Для этого включите полётный контроллер, нажмите на кнопку «Подключить» и далее в окне настроек нажмите на кнопку «Save Default». После этого текущие настройки сохранятся на флеш-память полётного контроллера. Для проверки откройте окно лога и в нём должна быть соответствующая запись. Далее на смартфоне в мобильном приложении вы можете нажать на кнопку «Load Default» для загрузки настроек по умолчанию из флеш-памяти полётного контроллера. Также вы можете всегда загрузить настройки по умолчанию на ноутбуке, нажав на кнопку «Load Default» в окне настроек. Далее нажмите на кнопку «Save», чтобы сохранить загруженные настройки по умолчанию на диске вашего ноутбука или смартфона, чтобы автоматически их использовать при следующем подключении.

На диске настройки сохраняются в файл в формате JSON. Файлы с настройками находятся в папке profiles внутри папки программы управления. Файл с настройками называется профилем. Текущий профиль можно изменить в окне настроек в выпадающем списке, который находится в левом верхнем углу окна настроек. Таким образом можно хранить настройки для разных моделей дронов и менять их в зависимости от запускаемой модели.

Внимание: Перед запуском модели проверяйте, что загружен правильный профиль, именно для той модели, которую вы запускаете!

Если вы изменили ту или иную настройку в момент, когда модель выключена, то нажмите на кнопку «Save», чтобы ваши изменения сохранились на диск. Если вы хотите изменить настройки во время, когда модель включена и установлена связь, то измените соответствующий нужный вам параметр, а затем нажмите на кнопку «Send», чтобы новые настройки были отправлены на полётный контроллер. После этого в окне настроек снова откройте тот параметр, который вы изменили и убедитесь в том, что его значение то, которое вы задавали. Иногда настройки могут не пройти передачу по WiFi сети, тогда в этом случае в окне настроек вы увидите старое значение параметра. Если значение нового параметра вас устраивает, то не забывайте нажимать на кнопку «Save» для сохранения настроек на диск.

# Настройка подключения к сети WiFi

При первом запуске данный полётный контроллер пытается подключиться к WiFi сети со следующими параметрами:

ssid = cicada

psk = cosmos327

gateway = 192.168.43.1

mask = 255.255.255.0

ip = 192.168.43.243

Поэтому для первого запуска вам необходимо изменить конфигурацию вашего wifi-роутера на параметры, указанные выше, либо создать новую wifi-сеть на ноутбуке с параметрами указанными выше. После этого запустите десктоп-приложение и нажмите на кнопку «Подключить».

Внимание: Для запуска десктоп-приложения на ноутбуке или ПК необходимо установить среду исполнения java-программ JRE v7 или выше

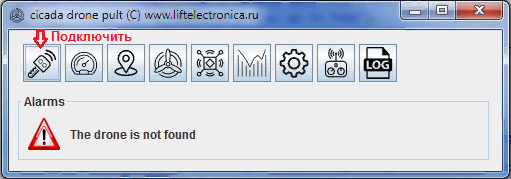
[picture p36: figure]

Если вы правильно настроили wifi-сеть, то подключение будет успешным, но сразу после подключения в окошке «Alarms» скорее всего будет сообщение о какой-либо ошибке. Это нормально для первого подключения так как ещё не настроены датчики.

Внимание: Если полётному контроллеру не удаётся подключиться к указанной сети WiFi, то полётный контроллер сам создаёт сеть WiFi как точка доступа.

Далее если вы хотите изменить сетевые настройки, то откройте окно настроек и измените сетевые настройки в разделе «Net» на те, которые вам требуются. Чтобы новые настройки вступили в силу, необходимо нажать на кнопку «Send». Далее, чтобы убедится в том, что новые настройки wifi-сети приняты и сохранены в полётном контроллере откройте окно лога и найдите, соответствующую запись, что новые сетевые настройки сохранены. Далее нажмите на кнопку «Save», чтобы сохранить новые настройки на диске вашего компьютера.

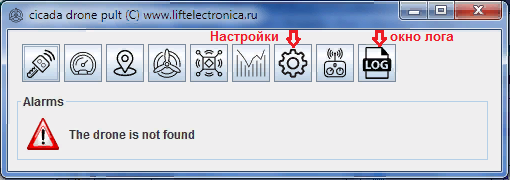
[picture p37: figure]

Внимание: Новые сетевые настройки будут применены только после сброса питания. Если у полётного контроллера не получается подключиться к новой wifi-сети, то после 5 попыток (5 секунд на попытку), то он сам создаст WiFi сеть как точка доступа с параметрами ssid=cicada, psk=cosmos327, gateway=192.168.43.1 ip=192.168.43.243, subnet = 255.255.255.0

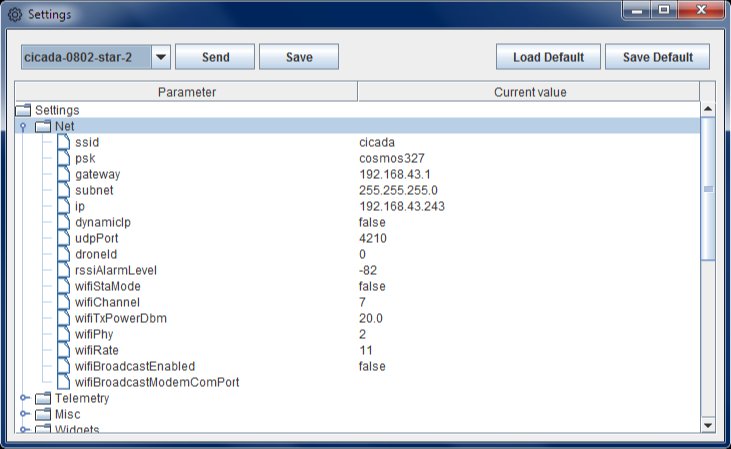
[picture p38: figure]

В одной wifi-сети могут работать сразу несколько полётных контроллеров. Для этого установите свой ip-адрес для каждого полётного контроллера в настройках взамен ip-адреса 192.168.43.243, который используется по умолчанию.

Если вы хотите подключить полётный контроллер к точке доступа, созданной мобильным устройством на Android, то сначала через десктоп-приложение установите ip-адрес 192.168.43.206 и gateway 192.168.43.1 или установите подключение с получением динамического ip-адреса. Для этого в настройках в разделе «Net» установите параметр «dynamicIp» как true. После подключения полетного контроллера к точке доступа посмотрите в настройках точки доступа выданный ему ip-адрес и запишите этот ip-адрес в настройках в разделе «Net»

Полётный контроллер позволяет настраивать режим работы WiFi модема. Для этого предназначены следующие параметры:

wifiStaMode когда этот параметр true, то полётный контроллер работает как станция WiFi и при старте старается подключиться к вашему роутеру. Когда этот параметр false, то полётный контроллер работает как точка доступа WiFi

wifiChannel номер канала WiFi в режиме работы как точка доступа, может быть от 1 до 11

wifiTxPowerDbm максимальная излучаемая мощность передатчиком в дБм. Максимум может быть 20 дБм, что соответствует 100 мВт

wifiPhy стандарт IEEE802.11 в котором работает точка доступа, созданная полётным контроллер. Может принимать следующие значения:

1 — для работы в режиме стандарта IEEE802.11B

2 – для работы в режиме стандарта IEEE802.11G

wifiRate – максимальная скорость передачи данных. Может принимать значения:

8 — 48 Мбит/с

9 — 24 Мбит/с

10 — 12 Мбит/с

11 — 6 Мбит/с

12 — 36 Мбит/с

13 — 54 Мбит/с

14 — 18 Мбит/с

15 — 9 Мбит/с

Полётный контроллер может работать не только в обычном режиме как станция WiFi или точка доступа WiFi, но также и в режиме WiFi Broadcast. Ещё этот режим называют WiFi Monitor. В данном режиме пакеты IEEE802.11 передаются и принимаются без процедуры регистрации в какой-либо сети. Для работы в этом режиме к ПК или Смартфону необходимо подключить специальный модем. Для того, чтобы несколько полётных контроллеров могли работать на одном канале WiFi одновременно необходимо, чтобы в этом случае параметр droneId у этих контроллеров был разным.

# Настройка и проверка моторов

Настройка моторов находится в окне настроек в разделе «Motors» и содержит следующие параметры:

- count – количество моторов на модели, этот параметр всегда должен быть равен 4
- maxGas – максимальная скорость вращения моторов в условных единицах
- minGas – минимальная скорость вращения моторов в условных единицах, пока этот параметр всегда должен быть равен 0
- esc – задаёт тип и протокол связи с регулятором оборотов. Может принимать следующие значения:
  - 0 — регуляторы оборотов с протоколом DSHOT-300, установите при этом maxGas = 1999
  - 10 — регулятор оборотов TeenyPro5A DSHOT-300, установите при этом maxGas = 1999
  - 20 — ШИМ 2.5КГц для управления коллекторными двигателями, установите при этом maxGas = 1999
  - 21 — ШИМ 5КГц для управления коллекторными двигателями, установите при этом maxGas = 1000
  - 22 — ШИМ 10КГц для управления коллекторными двигателями, установите при этом maxGas = 500
  - 23 — ШИМ 20КГц для управления коллекторными двигателями, установите при этом maxGas = 250
  - 24 — ШИМ 40КГц для управления коллекторными двигателями, установите при этом maxGas = 125
  - 25 — ШИМ 50КГц для управления коллекторными двигателями, установите при этом maxGas = 100

Внимание: Если у вас установлен оптический датчик смещения PMW3901, то управление коллекторными двигателями ШИМ сигналом невозможно, потому что сигнал разрешения ШИМ и SPI делят один и тот же пин. Поэтому не ставьте датчик PMW3901 на системы с коллекторными двигателями!

- frame – тип рамы. Может принимать следующие значения:
  - 0 – рама типа X или H с реверсивной схемой установки моторов (верхний левый мотор вращается против часовой стрелки)
  - 1 — рама типа X или H (верхний левый мотор вращается по часовой стрелке)

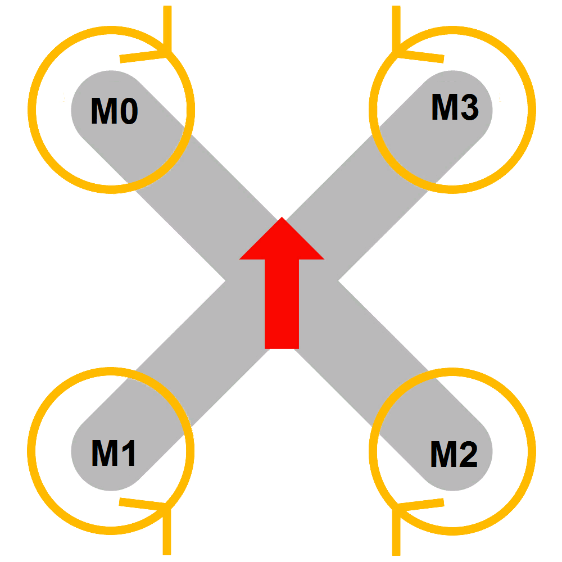
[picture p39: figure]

  - 2 — рама типа «крест»
  - 3 — рама типа «крест» с реверсивной схемой установки моторов

Для проверки моторов откройте окно управления моторами.

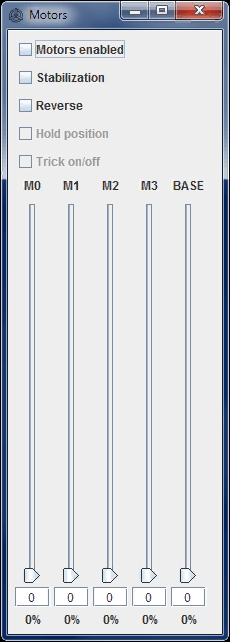
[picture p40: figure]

Чтобы проверить тот или иной двигатель установите флажок «Motors enabled». При этом если у вас регулятор оборотов с прошивкой BLHeli, то после установки флажка «Motors enabled» регулятор оборотов должен издать два длинных звука, что говорит о том, что моторы готовы к работе. Затем меняйте значение скорости вращения каждого мотора при помощи соответствующего слайдера. Слайдер «Base» позволяет задать одинаковую скорость вращения сразу для всех моторов.

Проверьте, что все моторы на вашей модели установлены в правильном порядке. При изменении М0 должен вращаться передний левый мотор, при изменении М1 — задний левый мотор, при изменении М2 — правый задний мотор и при изменении М3 — передний правый мотор.

Флажок «Stabilization» включает/выключает ПИД-регуляторы и алгоритмы стабилизации. Данный флажок включается автоматически, когда включен флажок «Motors enabled» и вы подаёте команду «Вверх» с пульта управления. Но также вы можете включать этот флажок вручную, но это не рекомендуется. Сразу как только вы включите этот флажок модель начинает принимать команды с пульта.

Флажок «Reverse» включает/выключает реверс двигателей и моторы вращаются в обратном направлении.

Внимание: Реверс работает только для бесколлекторных двигателей по протоколу DSHOT300. Для коллекторных двигателей с прямым управлением ШИМ сигналом реверс не работает!

Флажок «Hold position» нельзя изменить. Он служит только для индикации того, что модель находится в режиме удержания позиции.

Флажок «Trick on/off» нельзя изменить. Он служит только для индикации того, что модель находится в режиме выполнения трюков. В этом режиме отключены все ПИД-регуляторы, кроме ПИД-регуляторов угловых скоростей. В других полётных контроллерах этот режим называется «Акро».

# Датчики

При включении питания полётный контроллер автоматически определяет какие датчики к нему подключены. При этом у датчиков есть приоритет. Например, если вы пытаетесь подключить к полётному контроллеру два лидара или два магнетометра, то полётный контроллер будет опрашивать и работать только с одним лидаром или магнетометром у которого выше приоритет. Ниже приведен список приоритетов, если тот или иной датчик выше в списке значит у него выше приоритет.

1. Гироскоп
  - MPU9250
  - MPU6500
  - MPU6050
2. Акселерометр
  - MPU9250
  - MPU6500
  - MPU6050
3. Магнетометр
  - QMC5883L
  - MPU9250
4. Высотомер
  - TF Mini Plus
  - VL53L1X
  - HCSR04
5. Барометр
  - BMP280
6. Другие датчики и устройства, которые делят одни и те же ресурсы
  - PMW3901
  - ШИМ для коллекторных двигателей (сигнал разрешения включения двигателей подключается к 6 пину (GPIO12) модуля ESP8266)
  - Сервопривод для управления углом наклона камеры (подключается к 5 пину (GPIO14) модуля ESP8266)
  - Камера Runcam Split4 (Runcam-TX подключается к 6 пину (GPIO12), Runcam-RX подключается к 7 пину (GPIO13))

Гироскоп, акселерометр и магнетометр требуют настройки. Настройка этих датчиков описана в соответствующих главах этого документа. При установке полётного контроллера на модель ось X этих датчиков должна совпадать с направлением вперед.

Внимание: Магнетометр рекомендуется устанавливать на расстоянии минимум 50мм от проводов, идущих к двигателям и к батарейке. Если у вас полётный контроллер с imu-модулем MPU9250, в который встроен магнетометр, то в этом случае весь полётный контроллер рекомендуется устанавливать на модель как можно дальше от проводов, идущих к двигателям и батарее.

Барометр не требует настройки. Барометр используется для определения высоты полёта и стабилизации вертикальной скорости модели.

Внимание: Полётный контроллер с барометром рекомендуется устанавливать как можно дальше от пропеллеров или на уровне выше пропеллеров. Так как воздушные потоки под пропеллерами и рядом с ними создают сильные помехи для барометра. Также барометр следует защищать от воздействия солнечных лучей.

Высотомер и оптический датчик смещения не требуют настройки. Оптический датчик следует устанавливать на модель как показано на картинке ниже.

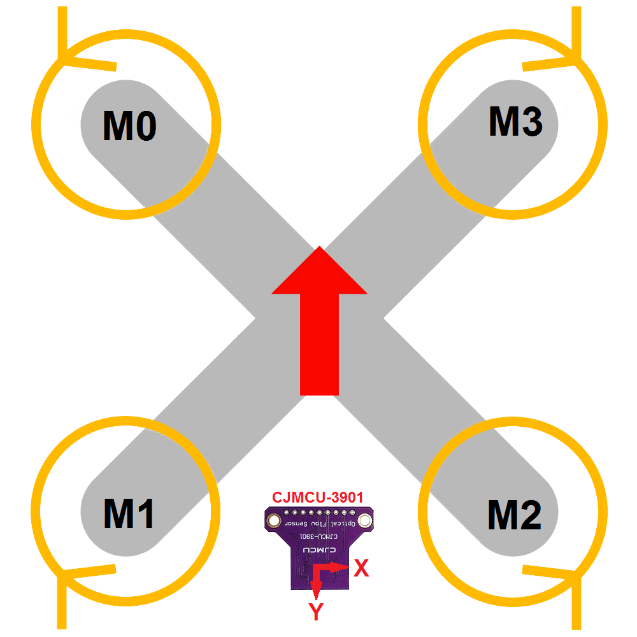
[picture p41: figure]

Магнетометр QMC5883L, который обычно встроен в модуль GPS, следует устанавливать как на картинке, показанной ниже.

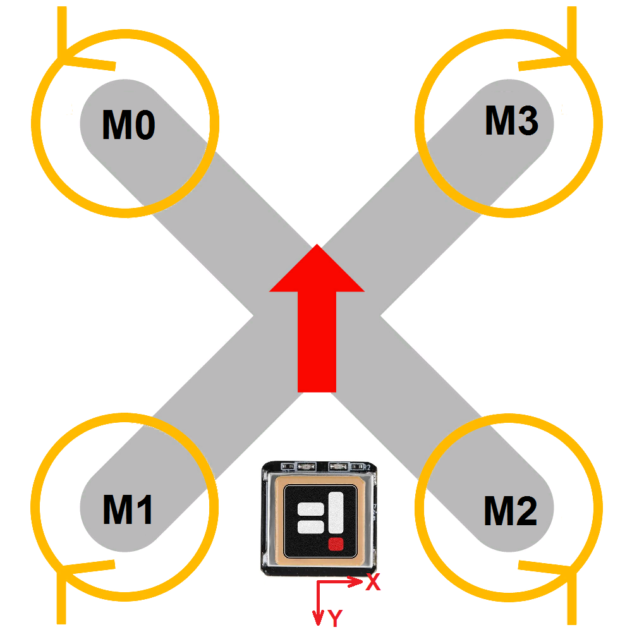
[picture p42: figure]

Навигационный приёмник GPS также не требует настройки. Для полётов внутри помещения следует отключать навигационный приёмник. Для этого в настройках в группе «GPS» для поля «enabled» следует написать false.

# Настройка гироскопа и акселерометра

Гироскоп — это самый главный датчик для квадрокоптера! Ни один квадрокоптер не может летать без гироскопа! Гироскоп измеряет скорости вращения квадрокоптера относительно локальных осей, что позволяет стабилизировать квадрокоптер. Практически все квадрокоптеры гражданского применения используют гироскопы, выполненные по технологии МЭМС (микроэлектронные механические системы). Данные гироскопы требуют настройки смещения нуля. Для этого включите ваш квадрокоптер и установите его на ровную параллельную поверхности Земли поверхность, например, на пол внутри помещения. Параллельность поверхности можно проверить и настроить при помощи строительного уровня. Далее откройте окно проверки и настройки трех-осевых датчиков.

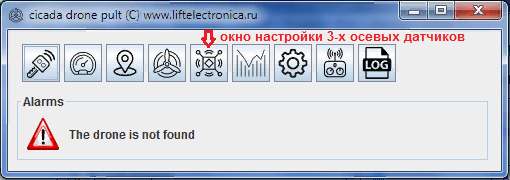
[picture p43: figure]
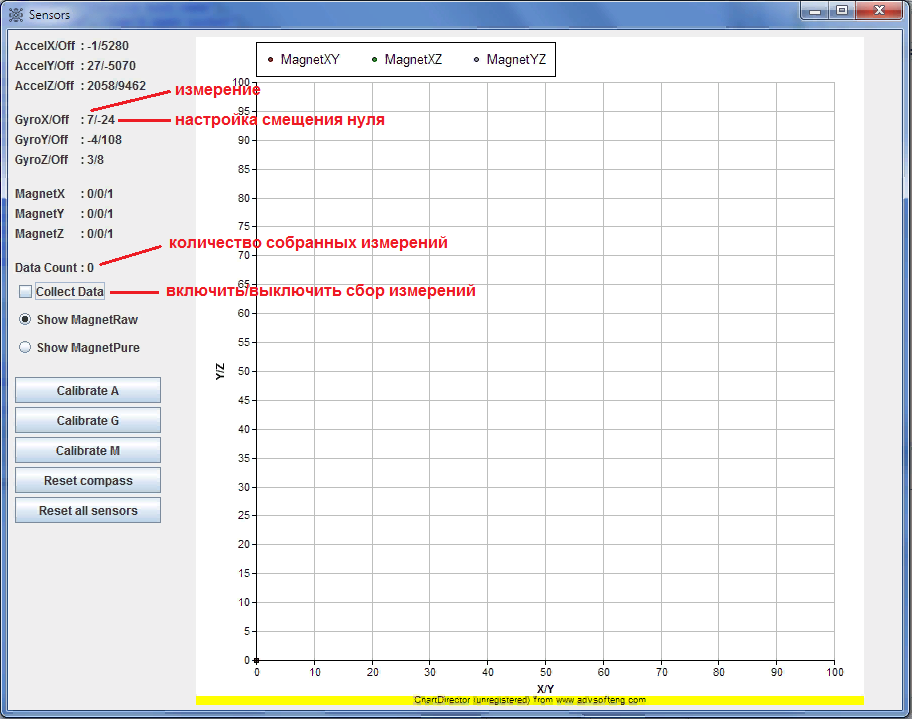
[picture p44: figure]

Цель настройки гироскопа заключается в том, чтобы измерения, сделанные гироскопом в состояния покоя, колебались относительно нуля. То есть число, которое подписано на картинке как «измерение», должно принимать значение, например, 0, -1, 1, -2, 0. Если это число больше чем 10, то гироскоп не настроен. Установите флажок «Collect Data» и ждите, когда значение поля «Data Count» станет 1024. После этого нажмите на кнопку «Calibrate G» для калибровки гироскопа. В это время программа посчитает новые значения смещения нуля и передаст их вашему квадрокоптеру. Если после выполнения данной операции, измерения гироскопа по-прежнему больше чем 10, то откройте окно настроек. В окне настроек в разделе «Gyroscope» установите для полей «offset» значения 0 и нажмите на «Send». Затем выполните процедуру калибровки гироскопа заново. Или прибавьте +10 или -10 к тому или иному значению «offset» и нажмите на «Send». Затем посмотрите как изменились данные от гироскопа в окне датчиков. Таким образом можно вручную подгонять настройку гироскопа.

Откройте окно настроек, после того как получится настроить смещение нуля для гироскопа. В разделе «Gyroscope» для полей «offset» запишите значения, которые записаны в окне настройки датчиков через слеш (на картинке выше подписано красным «настройка смещения нуля»). Далее сохраните новые настройки, нажав на кнопку «Save».

Внимание: Проверяйте настройку гироскопа перед каждым полётом! Хорошие гироскопы обычно сохраняют свои настройки смещения нуля. Но настройки некачественных гироскопов могут меняться от старта к старту и от температуры окружающей среды.

Далее в окне настроек в разделе «Gyroscope» есть параметр «dlpf». Этот параметр определяет частоту среза фильтра нижних частот.

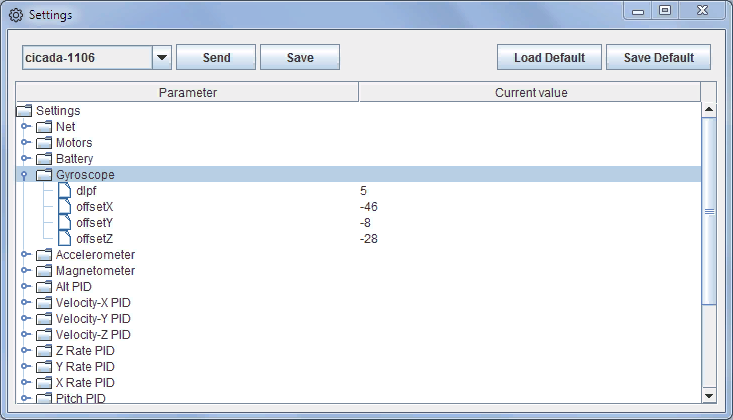
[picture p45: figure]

Чем ниже частота среза, тем меньше помех в сигнале от гироскопа, но квадрокоптер при этом становится более инертным, плохо стабилизируется и туго реагирует на команды. Чем выше частота среза, тем больше помех в сигнале от гироскопа. Квадрокоптер при этом стабилизируется лучше, но при этом выше шумы на двигателях из-за чего они сильнее нагреваются. Рекомендуется этот параметр установить равным 5 и не менять. В таблице ниже приведены значения параметра dlpf и соответствующие ему частоты среза фильтра нижних частот для гироскопов MPU9250, MPU6500. Для других модулей IMU ищите данную информацию в даташитах.

Значение dlpf | Частота среза ФНЧ
0 | 250 Гц
1 | 184 Гц
2 | 92 Гц
3 | 41 Гц
4 | 20 Гц
5 | 10 Гц
6 | 5 Гц

Внимание: Если вы измените параметр dlpf, то вам потом потребуется заново настраивать ПИД-регуляторы угловых скоростей.

Далее необходимо настроить акселерометр. Акселерометр участвует в расчете крена (roll) и тангажа (pitch), позволяет определить линейные скорости перемещения.

Внимание: На полёт в режиме Акро, когда включена только стабилизация угловых скоростей, акселерометр не влияет! Акселерометр включается в режиме удержания горизонта и других выше стоящих режимах стабилизации.

Цель настройки акселерометра такая же как и для гироскопа: значения измерений по осям X и Y должны колебаться около нуля, а вот значение измерения по оси Z должно колебаться около 2048. Процедура настройки акселерометра точно такая же как и для гироскопа. Установите модель на ровную поверхность параллельную поверхности Земли. Нажмите на «Collect Data». После того как «Data Count» досчитает до 1024 нажмите на «Calibrate A». Если после калибровки значения измерений по осям X,Y больше чем 100, то откройте окно настроек и точно так же как для гироскопа установите значения параметров «offset» для акселерометра равными нулю и повторите процедуру настройки. Или прибавьте +10 или -10 к тому или иному значению «offset» и нажмите на «Send». Затем посмотрите как изменились данные от акселерометра в окне датчиков. Таким образом можно вручную подгонять настройку акселерометра.

Далее в окне настроек в разделе «Accelerometer» есть параметр «dlpf». Точно также как для гироскопа этот параметр определяет частоту среза фильтра нижних частот акселерометра. Рекомендуется этот параметр не изменять и оставить равным 6. Если изменить этот параметр, то потом придётся перенастраивать ПИД-регуляторы угловых скоростей. В таблице ниже приведены значения параметра dlpf и соответствующие ему частоты среза фильтра нижних частот для акселерометров MPU9250, MPU6500. Для других модулей IMU ищите данную информацию в даташитах.

Значение dlpf | Частота среза ФНЧ
0 | 218 Гц
1 | 218 Гц
2 | 99 Гц
3 | 45 Гц
4 | 21 Гц
5 | 10 Гц
6 | 5 Гц

Если при взлете модель начинает кренить в сторону без команды, то скорее всего на акселерометре сильные помехи. Это можно проследить по данным телеметрии. Для устранения проблемы попробуйте:

- Установите полётный контроллер на резиновые стойки или приклейте полётный контроллер к раме на двусторонний скотч
- Отбалансируйте пропеллеры и уменьшите вибрации от двигателей
- Делайте резкий взлёт
- Защитите полётный контроллер от воздействия лучей Солнца
- В окне настроек в разделе «Kalman Filter» установите параметр «pitchRollRateVariance» = 0,0013 и параметр «accPitchRollVariance» = 0,02 Используйте этот вариант решения, только если другие варианты не помогли, так как этот вариант уменьшает точность вычисления крена и тангажа!

Если в полёте в режиме удержания горизонта при отпускании стиков пульта управления квадрокоптер сильно тянет в ту или иную сторону, то необходимо подогнать параметр «offset» в окне настроек для акселерометра, прибавив +10 или -10 или другое значение. Если квадрокоптер тянет вперёд или назад, то необходимо играть с параметром «offsetX» для акселерометра. Если влево или вправо, то с параметром «offsetY».

# Настройка магнетометра

Магнетометр используется на квадрокоптере для точного определения азимута. Азимут — это угол между направлением на север и направлением в котором повернута модель. Знать этот угол необходимо для реализации стабилизации по GPS и другим спутниковым навигационным системам, так как все навигационные системы определяют скорости движения относительно направления на север и восток и эти скорости необходимо преобразовывать в локальную систему координат дрона.

Настройка магнетометра выполняется в окне настройки 3-х осевых датчиков. Откройте этот окно и включите флажок «Collect data». После этого поверните вашу модель руками вокруг оси X пять раз, далее вокруг оси Y и Z тоже по пять раз. Затем вращайте произвольно во всех направлениях пока поле «Data count» в окне настройки датчиков не станет равным 1024. В то время когда вы вращаете вашу модель идёт сбор данных с магнетометра. После того как сбор данных закончен нажмите на кнопку «Calibrate M» для калибровки магнетометра. Далее следует проверить качество калибровки. Снова включите флажок «Collect data» и вращайте модель руками во всех направлениях пока поле «Data count» не станет равным 1024. После этого включите флажок «Show MagnetPure». Если магнетометр откалибровался правильно, то все точки должны лежать внутри одной окружности.

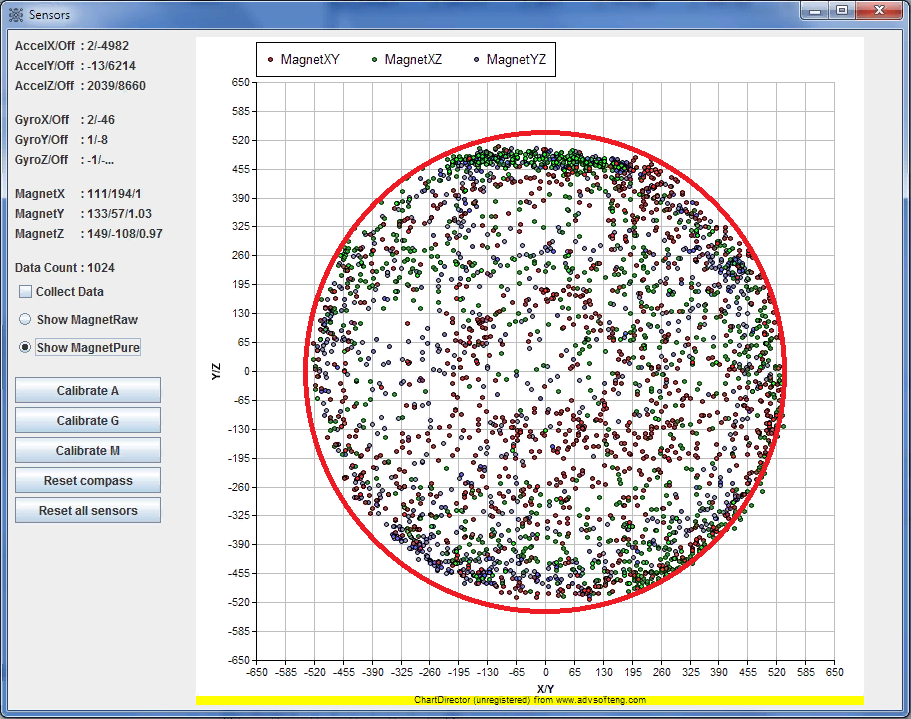
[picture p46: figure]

Если это не так и точки сильно разбросаны, то следует открыть окно настроек. В разделе «Magnetometer» для параметров «offset» установить значение 0, а для параметров «scale» установить значение 1. Или в окне настройки датчиков нажать на кнопку «Reset compass». Затем повторить процедуру калибровки как описано выше.

Внимание: Калибровку магнетометра следует проводить вдали от массивных металлических объектов и линий электропередач, так как они искажают магнитное поле Земли вокруг себя.

Если процедура калибровки магнетометра выполнена успешно, то следует переписать значения полей «offset» и «scale» из окна настройки датчиков в раздел «Magnetometer» в окне настроек и сохранить новые настройки, нажав на кнопку «Save».

Параметр «declination» - это магнитное склонение для вашей области в радианах. Его можно узнать в интернете. Обратите внимание, что в интернете он будет указан в градусах, но вам нужно будет его преобразовать в радианы и записать в настройки. После этого для проверки поверните вашу модель руками точно на север и проверьте в окне «Status», что угол «Yaw» равен 0 градусов. Чтобы повернуть модель точно на север используйте магнитный компас, при этом не забудьте учесть магнитное склонение!

На показания магнетометра очень сильно влияют электродвигатели так как электрический ток, который течет по проводам от электродвигателей создаёт вокруг себя сильное магнитное поле, которое искажает измерения магнетометра. Поэтому рекомендуется размещать магнетометр как можно дальше от проводов, которые идут к электродвигателям на дистанции не менее 50мм. Если этого сделать не получается, то после взлёта посмотрите на сколько изменяется значение азимута от работающих двигателей и запишите эту разницу в параметр «inflightCorrection» в настройках магнетометра. Значение этого параметра также нужно записывать в радианах.

# Режимы стабилизации полёта

В отличие от других моделей полётных контроллеров в данном полётном контроллере нет такого параметра как режим стабилизации. Все режимы создаются путем включения тех или иных ПИД-регуляторов.

Режим «Акро» - для полёта в этом режиме откройте окно настроек и выключите ПИД-регуляторы для стабилизации по углам Эйлера - это HeadingPID, PitchPID, RollPID. Для этого параметр «enable» для каждого из этих ПИД-регуляторов установите как «false». Далее если хотите, то можете сохранить текущий профиль, добавив к названию слово acro, например, cicada-1404fr-acro, чтобы в следующий раз можно было быстро включить этот режим. В этом режиме если модель у вас летела вперёд или назад, то после отпускания стиков она так и продолжит лететь с тем же самым креном или тангажом. Данный режим очень труден для управления и используется для выполнения фигур высшего пилотажа.

Внимание: Для всех ниже описанных режимов ПИД-регуляторы PitchPID и RollPID должны быть всегда включены. ПИД-регуляторы X Rate PID, Y Rate PID, Z Rate PID должны быть включены всегда!

Режим «Горизонт» - для полёта в этом режиме включите HeadingPID, PitchPID, RollPID и отключите Velocity-X PID и Velocity-Y PID. Далее также можете сохранить отдельный профиль, например, cicada-1404fr-hor, чтобы потом быстро можно было включить этот режим. В данном режиме после отпускания стиков на пульте управления модель будет стремиться удерживать тангаж и крен равными нулю. Но при этом, если модель до этого у вас двигалась вперед и назад, то после выравнивания она так и продолжит движение согласно первому закону Ньютона, но постепенно будет останавливаться из-за торможения воздухом, а после остановки будет дрейфовать (случайно лететь в какую-либо сторону с небольшой скоростью). Модель будет дрейфовать из-за небольших дуновений ветра и точности работы и настройки акселерометра.

Режим стабилизации «горизонтальной скорости». Если вы хотите, чтобы модель после отпускания стиков останавливалась быстрее и потом стояла на месте, то включите ПИД-регуляторы Velocity-X PID и Velocity-Y PID. Но если, например, будет дуть ветер, то модель будет ему сопротивляться, стараясь удерживать свою горизонтальную скорость равную нулю, но при этом из-за небольших перемещений будет терять позицию и обратно в нее не вернется.

Внимание: Режим стабилизации горизонтальной скорости возможен только если на вашей модели установлен GPS+магнетометр или оптический датчик смещения + дальномером (лидар/сонар). Либо и то и другое.

Режим «удержания позиции». Для работы этого режима необходимо включить Velocity-X PID, Velocity-Y PID, PosNorthPID, PosEastPID. Точно также как для режима стабилизации горизонтальной скорости на вашей модели должны быть установлены те же датчики, что и для режима стабилизации горизонтальной скорости.

Режим стабилизации «вертикальной скорости». Для включения этого режима включите ПИД-регулятор Velocity-Z PID. В этом режиме модель будет стремиться удерживать свою вертикальную скорость равную нулю после отпускания стика управления газом. При этом модель будет сохранять свою высоту некоторое время, но если подует ветер, то модель изменит высоту, а также модель будет дрейфовать по высоте из-за качества работы барометра и акселерометра.

Внимание: Режим стабилизации вертикальной скорости возможен только если на вашей модели установлен барометр или дальномер либо оба датчика сразу.

Режим удержания «высоты». Для работы этого режима необходимо включить Velocity-Z PID и Alt PID. Точно также как для режима стабилизации вертикальной скорости на вашей модели должны быть установлены те же датчики, что и для режима стабилизации вертикальной скорости.

# Настройка ПИД-регуляторов, телеметрия

Пропорционально-интегрально-дифференциальный регулятор (ПИД) – это алгоритм для автоматического поддержания в заданном интервале одного или нескольких параметров. При помощи ПИД-регуляторов можно реализовать любые законы регулирования.

Квадрокоптер — это не стабильный летательный аппарат. И если включить двигатели без алгоритмов стабилизации, то квадрокоптер будет вращаться и лететь в сторону в произвольном направлении или просто перевернётся вверх-ногами. Для стабилизации и управления квадрокоптером служат ПИД-регуляторы. Все ПИД-регуляторы объединяются в цепочку. Таким образом сигнал от ПИД-регулятора верхнего уровня поступает на ПИД-регулятор нижнего уровня, а далее с этого ПИД-регулятора на ПИД-регулятор, который находится ещё ниже уровнем.

Процесс стабилизации можно разделить на уровни.

- Стабилизация 1 уровня. Здесь работают ПИД-регуляторы удержания угловых скоростей вращения на заданном уровне. Это самый нижний уровень стабилизации и отсюда выходный сигнал с ПИД-регуляторов непосредственно задаёт скорость вращения того или иного мотора. В настройках это Z Rate Pid, Y Rate Pid, X Rate Pid
- Стабилизация 2 уровня. Автопилот. На этом уровне работают ПИД-регуляторы стабилизации по курсу, крену и тангажу. В настройках это Heading Pid, Pitch Pid, Roll Pid. Сигналы с этих ПИД-регуляторов поступает на ПИД регуляторы 1 уровня. Данную стабилизацию уже можно назвать «Автопилотом» и все последующие уровни стабилизации также относятся к автопилоту.
- Стабилизация 3 уровня. На этом уровне работают ПИД-регуляторы стабилизации линейных скоростей. В настройках это Velocity-X Pid, Velocity-Y Pid, Velocity-Z Pid.
- Стабилизация 4 уровня. На этом уровне работают ПИД-регуляторы удержания позиции и высоты. В настройках это Alt Pid, Pos North Pid, Pos East Pid.

Задача каждого ПИД-регулятора заключается в том, чтобы выдать такое воздействие, чтобы регулируемая им величина соответствовала заданной. Например, мы хотим повернуть наш квадрокоптер вокруг оси Z с определенной скоростью, чтобы изменить курс. Для этого с пульта управления при нажатии на соответствующую кнопку на ПИД-регулятор Z Rate Pid поступает задание, что мы хотим вращать модель с такой то скоростью. Регулятор принимает это задание и начинает менять скорость вращения моторов CW и CCW до тех пор, пока скорость вращения самого квадрокоптера не станет заданной. Для этого регулятор непрерывано следит за изменением скорости вращения квадрокоптера, которая поступает к нему от датчика (гироскопа). Вторая задача ПИД-регулятора — это выдать такое воздействие, чтобы заданная скорость вращения была достигнута в кратчайшее время. За всем этим можно следить через телеметрию и тем самым точнее подбирать параметры того или иного ПИД-регулятора. Так описанный процесс регулирования скорости вращения по оси Z при настроенном ПИД-регуляторе Z Rate Pid будет выглядеть примерно как на картинке ниже.

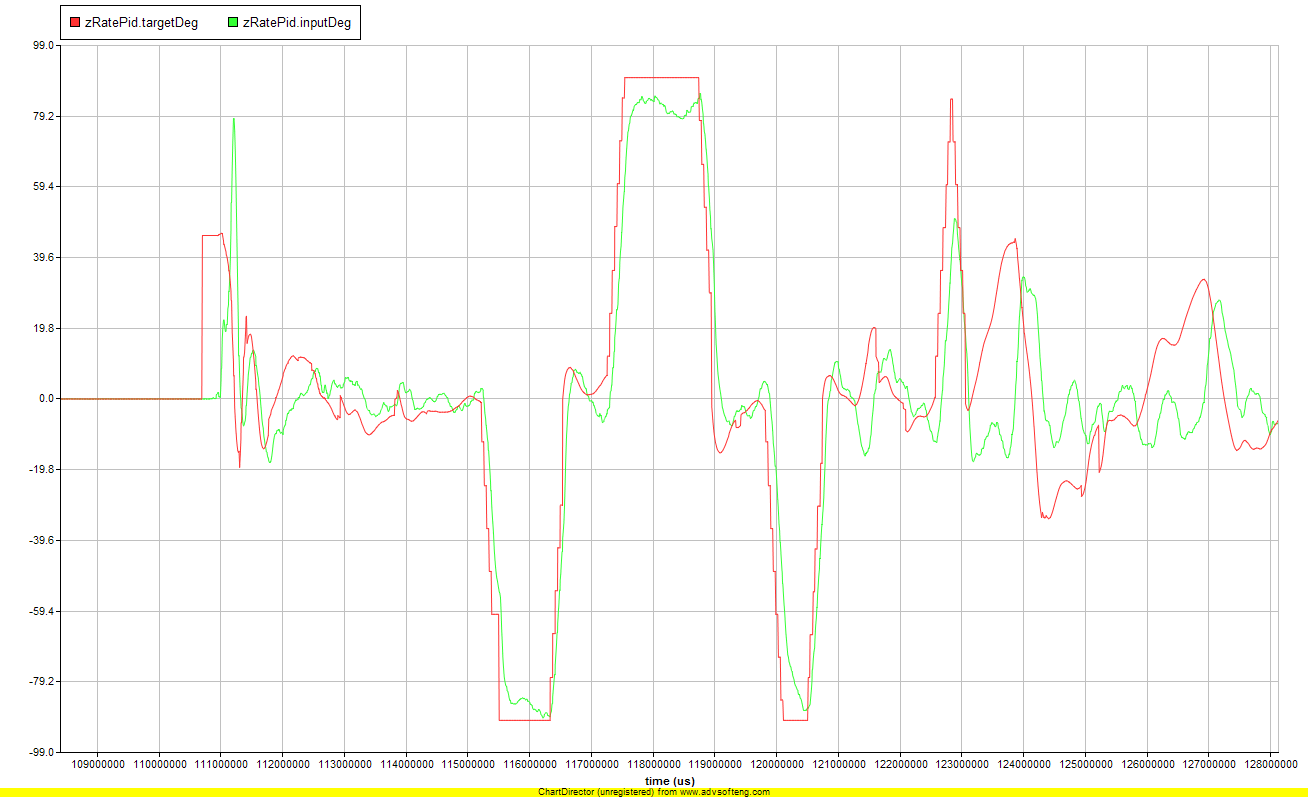
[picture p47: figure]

Здесь на этой картинке красной линией нарисовано задание для ПИД-регулятора (уставка), которое мы задаём с пульта управления. А зелёная линия — это реальная скорость вращения вокруг оси Z, измеренная гироскопом. В идеальном случае зелёная линия должна повторять красную. Но это только в иллюзорном идеальном мире. В реальном мире, чем ближе зеленая линия к красной - тем лучше настроен ПИД-регулятор.

Для того чтобы посмотреть телеметрию необходимо открыть окно телеметрии, нажав на кнопку «Charts»

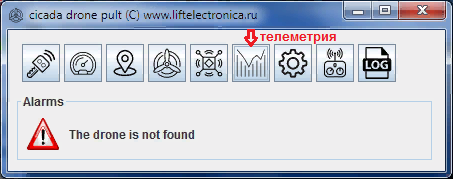
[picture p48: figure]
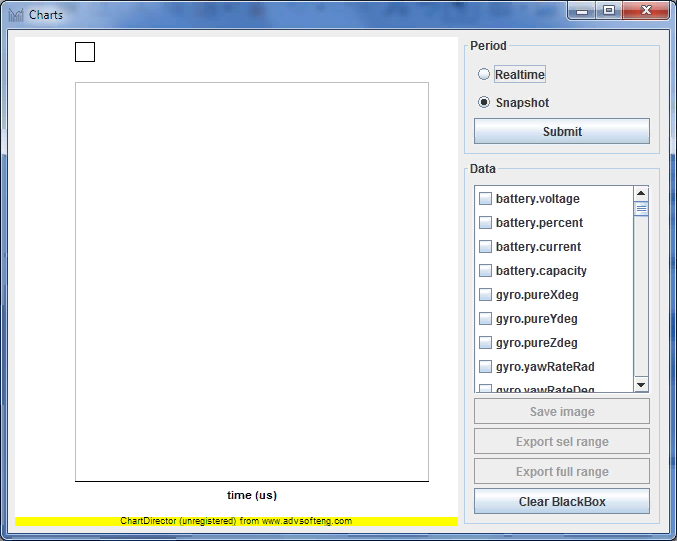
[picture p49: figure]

Чтобы обновить данные телеметрии нажмите на кнопку «Submit». За телеметрией можно следить в режиме реального времени. Для этого установите флажок «Realtime» и нажмите «Submit». Все параметры, которые передаются в телеметрии находятся в списке. Видимую картинку с графиком можно сохранить на диск в виде графического файла JPEG, PNG. Далее отмеченные в списке параметры можно сохранить в электронную таблицу CSV, нажав на кнопку «Export sel range» или «Export full range». Если щёлкнуть на графике левой кнопкой мыши, то можно выбрать диапазон для кнопки «Export sel range». Сохраненные таким образом параметры потом можно проанализировать в другом программном обеспечении. Например, в программе LibreOffice.Calc можно выполнить преобразование Фурье для сохраненных параметров и посмотреть спектр помех того или иного параметра.

Внимание: По умолчанию данные телеметрии передаются через каждые 10мс. Этот интервал можно изменить в настройках в разделе «Net» параметр telemetryPeriod, который задаётся в микросекундах.

Кнопка «Clear BlackBox» полностью удаляет все данные телеметрии и очищает «чёрынй ящик». После переключения питания квадрокоптера обязательно очищайте «чёрный ящик» нажатием этой кнопки, а также перед каждым полётом, если вам нужны данные телеметрии.

Внимание: Все данные телеметрии хранятся в ОЗУ вашего хоста (ноутбука). Полётный контроллер не каким образом не хранит телеметрию в своих запоминающих устройствах.

Далее перейдем к настройке ПИД-регуляторов. При установке полётного контроллера на свою модель сначала загрузите профиль default или скопируйте настройки ПИД-регулятора из этого профиля. Как правило, на новой модели нужно будет подобрать настройки только для трех ПИД-регуляторов первого уровня стабилизации — это Z Rate PID, X Rate PID, Y Rate PID. Настройки остальных ПИД-регуляторов подходят практически ко всем моделям и их можно не менять.

Для настройки ПИД-регуляторов угловых скоростей можно применять следующий алгоритм:

1. Включите режим стабилизации «Горизонт» и режим стабилизаци вертикальной скорости при наличи барометра на вашей модели.
2. Для ПИД-регуляторов X Rate Pid и Y Rate Pid установите kp=40, ki = 40, kd = 2
3. Для ПИД-регулятора Z Rate Pid установите kp = 200, ki = 100, kd = 0
4. Попробуйте взлететь на небольшую высоту. Если модель раскачивается, то приземлитесь и попробуйте уменьшить параметр kp на 2 для X Rate PID, Y Rate PID. И далее снова пробуйте взлетать и уменьшать kp до тех пор пока модель не прекратит раскачиваться. Если при первом взлете модель не раскачивалась, то, наоборот, попробуйте увеличить kp на 2 до тех пор пока модель не начнет раскачиваться, а потом уменьшите до значения при котором модель не раскачивается. То есть параметр kp должен быть ближе к критическому значению при котором модель раскачивается.
5. Если после настройки параметра kp модель при взлёте сильно летит в сторону, то увеличьте ki на 10, а также проверьте настройку акселерометра. Сильно увеличивать ki не стоит, так как модель будет хуже и дольше реагировать на команды.
6. После настройки параметра ki попробуйте полетать и после приземления посмотрите данные телеметрии. Проверьте по телеметрии значения параметров xRatePid.out и yRatePid.out. Если на графике много шумов, то следует уменьшить параметр kd на 0.5, если не так много, то можно увеличить для лучшей стабилизации.

Внимание: Перед настройкой ПИД-регуляторов обязательно должны быть настроены гироскоп и акселерометр.

У ПИД-регулятора вертикальной скорости Velocity-Z Pid есть параметр «takeoffErrSum» этот параметр задаёт начальное значение интегральной суммы для данного ПИД-регулятора, что позволяет делать резкий взлёт с земли в режиме стабилизации вертикальной скорости. Для того чтобы подобрать этот параметр выполните полёт, а потом по данным телеметрии посмотрите среднее значение параметра «velocityZPid.errSum». Данное среднее значение и запишите в настройках для параметра «takeoffErrSum». Если вы хотите, чтобы квадрокоптер взлетал не резко, то уменьшите этот параметр. Если хотите, чтобы взлетал резче, то увеличьте этот параметр.

# Управление

Для управления дроном откройте окно управления. Если это окно будет закрыто, то управление дроном будет не доступно.

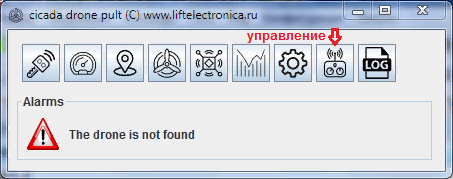
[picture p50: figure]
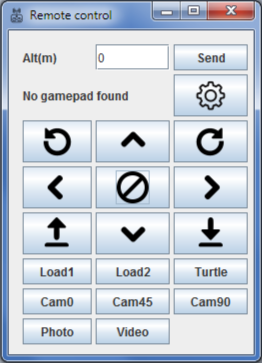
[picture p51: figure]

Управлять дроном можно щелкая мышью по кнопкам на экране (виртуальная клавиатура) либо с клавиатуры или геймпада. Поле «Alt(m)» и кнопка «Send» позволяют задать удерживаемую высоту для ПИД-регулятора высоты, если он включен у вас в настройках.

Внимание: Опрос устройств ввода (клавиатуры, геймпада) производится с частотой 25 Гц (через каждые 40 мс).

Для взлёта сначала включите двигатели, нажав на соответствующую кнопку или отметив флажок «Motors enabled» в окне моторов. Далее удерживайте кнопку «Вверх» (набрать высоту). При этом будут включены алгоритмы стабилизации и дрон начнёт стабилизироваться и набирать высоту. Включение стабилизации можно проследить, если в окне моторов будет отмечен флажок «Stabilization».

Для настройки управления с клавиатуры или геймпада откройте окно настройки управления, щёлкнув по кнопке с изображением зубчатого колеса.

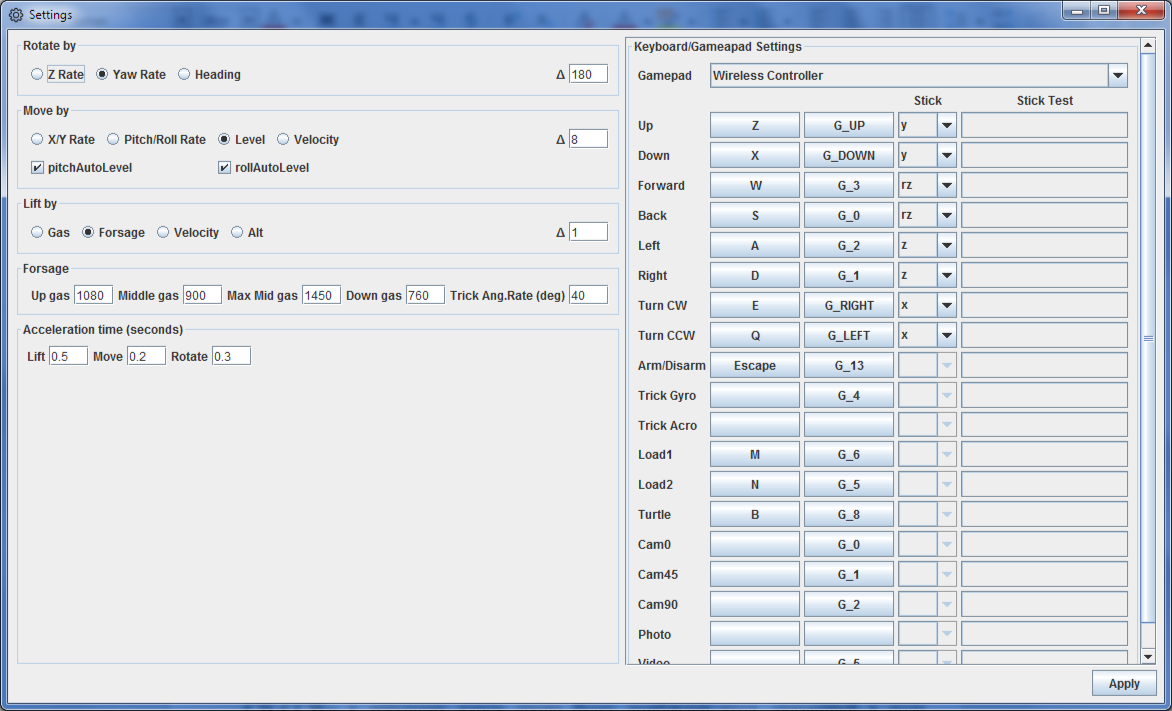
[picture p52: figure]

К каждой команде управления можно привязать две кнопки и один стик геймпада. Чтобы, например, изменить кнопку управления командой «Up» щёлкните сначала на экране на соответствующую кнопку, а затем нажмите на клавишу на клавиатуре или на геймпаде, которой вы хотите подавать данную команду.

В группе «Rotate by» задаётся режим управления по оси Z. При выборе режима «Yaw Rate» при подаче команд «Turn CW/CCW» дрон будет стараться набрать скорость вращения, указанную в поле «дельта» справа. Скорость вращения указывается в град/с. При выборе режима «Heading» при подаче команд «Turn CW/CCW» к текущему курсу дрона будет прибавлен угол, указанный в поле «дельта» справа. Угол указывается в градусах. Также для работы этого режима у вас должен быть включен «Heading PID» в настройках. Но данный режим управления не рекомендуется использовать даже если у вас включен «Heading PID». Далее если вы управляете дроном с клавиатуры ПК или виртуальной клавиатуры, то заданная скорость вращения будет подаваться с ускорением/замедлением, чтобы дрон набирал скорость вращения плавно. Время ускорения можно изменить в группе «Acceleration time» в поле «Rotate», которое находится ниже в данном окне. Время ускорения задаётся в секундах. Данный параметр не влияет, если вы управляете дроном при помощи стиков. При выборе режима «Z Rate» дрон будет стараться набрать скорость вращения относительно локальной оси Z, при этом при наличии сигнала управления будут на время действия этого сигнала будут отключены ПИД регуляторы углов Эйлера Pitch, Roll, Heading.

В группе «Move by» задаётся режим управления по перемещению. При выборе режима «X/Y Rate» при подаче команд «Forward/Back/Left/Right» дрон будет стараться набрать скорость вращения по локальным осям X,Y, указанную в поле «дельта» справа. Скорость вращения указывается в град/с. При этом если включены ПИД-регуляторы по крену и тангажу (Pitch PID, Roll PID) и выключены флажки «pitchAutoLevel» и «rollAutoLevel», то после отпускания стика или кнопки дрон будет стараться удерживать набранный крен или тангаж. В случае, когда Pitch PID, Roll PID включены в настройках и включены флажки «pitchAutoLevel» и «rollAutoLevel» то после отпускания стика или кнопки дрон будет стараться выровнять горизонт, когда крен и тангаж равны нулю. При выборе режима «Level» управление будет происходить по заданному крену и тангажу. При нажатии на кнопку или стик модель будет стараться набрать и удерживать крен/тангаж заданный в поле «дельта» справа. После отпускания кнопки или стика модель будет стараться выровнять горизонт, когда крен и тангаж равны нулю.

Внимание: Для управления в режиме «Level» в настройках должны быть включены Pitch PID, Roll PID. Это рекомендуемый режим управления.

При выборе режима «Velocity» управление будет происходить по заданным линейным скоростям. При нажатии на кнопку или стик дрон будет стараться набраться заданную скорость, которая указывается в поле «дельта» справа. Скорость указывается в м/с. При отпускании кнопки или стика дрон будет стараться удерживать скорость ноль, сопротивляясь ветру и другим факторам.

Внимание: Для управления в режиме «Velocity» в настройках должны быть включены Pitch PID, Roll PID, Velocity X PID, Velocity Y PID. На вашей модели должны быть обязательно установлены датчики оптического смещения и лидар либо GPS либо и то и другое.

Далее если вы управляете дроном с клавиатуры, то заданные угловая скорость, крен, тангаж, линейная скорость (в зависимости от выбранного режима перемещения) будут подаваться с ускорением/замедлением, которое задаётся в поле «Move» в группе «Acceleration». Время ускорения задаётся в секундах. Данный параметр не влияет, если вы управляете дроном при помощи стиков.

В группе «Lift by» задаётся управление высотой. При выборе режима «Gas» к текущему базовому газу при нажатии на кнопку или стик будет прибавляться число, указанное в поле «дельта» справа. При этом максимальный газ не сможет превысить число заданное в поле «Up gas» в группе «Forsage». Тоже самое касается и минимального газа. После отпускания кнопки или стика набранный газ так и останется на том же уровне. При выборе режима «Forsage» базовый газ будет также изменяться от минимального газа до максимального, заданных в группе «Forsage», но после отпускания кнопки или стика базовый газ будет устанавливаться на уровне, заданном в поле «Middle Gas» плюс поправка на уровень разряда батареи. Величина поправки настраивается установкой параметра «Max Middle Gas» - это величина среднего газа при минимальном уровне заряда батареи. При выборе режима «Velocity» управление высотой будет происходить по заданию вертикальной скорости. Максимальная вертикальная скорость указывается в поле «дельта» справа. Вертикальная скорость задаётся в м/с. При отпускании кнопки или стика дрон будет стараться удерживать вертикальную скорость равную нулю.

Внимание: Для управления в режиме «Velocity» в настройках должен быть включен Velocity Z PID . На вашей модели должны быть обязательно установлены барометр или лидар либо и то и другое. Это рекомендуемый режим управления высотой.

При выборе режима управления «Alt» к заданной высоте будет прибавляться число, указанное в поле «дельта» справа. Этот режим работает только если в настройках включен Alt PID и на модели установлены барометр или лидар или и то и другое. Далее если вы управляете дроном с клавиатуры, то заданные базовый газ, вертикальная скорость (в зависимости от выбранного режима перемещения) будут подаваться с ускорением/замедлением, которое задаётся в поле «Lift» в группе «Acceleration». Время ускорения задаётся в секундах. Данный параметр не влияет, если вы управляете дроном при помощи стиков.

Режим «Трюков» включается при удержании соответствующей клавиши, которая задаётся кнопкой «Trick on/off». В режиме трюков выключаются все ПИД-регуляторы кроме Z Rate PID, Y Rate PID, X Rate PID, а управление газом переходит в режим «Forsage». Максимальная угловая скорость, которая будет задаваться для Y Rate PID, X Rate PID, устанавливается в поле «Trick Ang.Rate (deg)» в группе «Forsage». А для Z Rate PID максимальная угловая скорость устанавливается в поле «дельта» группы «Rotate by». Как только вы отпустите кнопку «Трюки» все ПИД-регуляторы, которые были выключены будут включены снова и модель будет стараться вернуться в нормальное состояние.

Кнопка «Turtle» включает режим «анти-черепаха». Этот режим используется, когда ваша модель упала и лежит на земле вверх-ногами. При нажатии на эту кнопку поочередно будет включаться реверс сначала левых моторов, при следующем нажатии для правых и так далее, с целью перевернуть модель в нормальное положение.

Внимание: Режим «анти-черепаха» работает только при выключенной стабилизации (флажок stabilizationEnabled должен быть отключен, а флажок motorsEnabled должен быть, наоборот, включен). Этот режим доступен только для моделей с регулятором оборотов, которые работают по протоколу DSHOT300.

В настройках в группе «Motors» можно настроить уровень газа, который будет подаваться на моторы в режиме «анти-черепаха», для этого там есть параметр «antiTurtleGas»

Кнопки «Load1» и «Load2» включают нагрузки, которые несёт на себе модель. Нагрузка — это светодиодная лента, буззер и прочие устройства. Нагрузка может включаться/выключаться с некоторым периодом, который можно задать в настройках. Для этого в группе «Load» есть параметр «period». Если этот параметр равен 0, то пока удерживается одна из кнопок «Load», нагрузка будет включена постоянно. Если этот параметр больше 0, то пока удерживается одна из кнопок «Load», нагрузка будет включаться и выключаться с периодом, заданным этим параметром. Другими словами, нагрузка будет моргать. Период задаётся в миллисекундах.

Внимание: Нагрузки доступны только для модификаций cicada-main и cicada-mini.

Кнопки «Cam0» «Cam45» «Cam90» управляют углом наклона камеры, если на вашей модели установлен сервопривод.

Кнопка «Video» включает/выключает запись камеры на сд-карту. Для этого на вашей модели должна быть установлена соответствующая камера.

Кнопка «Photo» делает фото и сохраняет его на сд-карту.

Внимание: Камера Runcam Split4 не поддерживает фотографии

# Настройка фильтра Калмана

Фильтр Калмана — это математический, программный алгоритм, который объединяет показания различных датчиков и считает курс, крен, тангаж, вертикальную и горизонтальную скорость, координаты в мировой системе координат. Про работу фильтра Калмана написано много статей и книг, поэтому в этом руководстве принцип работы фильтра Калмана не описывается.

Внимание: Настройки по умолчанию для фильтра Калмана рекомендуется не менять!

Ниже приведен список параметров фильтра Калмана. Значения всех параметров подбираются экспериментально. Для каждого параметра есть простое правило. Чем выше значение параметра тем меньше фильтр Калмана доверяет показаниям того или иного датчика. Если датчик сильно шумит или врёт, то значение его параметра следует делать выше. А если, например, значение параметра установить равным 1000000, то фильтр Калмана практически не будет использовать показания данного датчика в расчетах, таким образом можно отключить датчик от системы. И соответственно чем меньше значение для параметра тем сильнее фильтр Калмана доверяет датчику.

Внимание: Фильтр Калмана очень плохо реагирует на выбросы в измерениях того или иного датчика: он воспринимает их как достоверные данные и резко меняет рассчитываемые параметры, чтобы они соответствовали выбросу. Поэтому следите за выбросами в измерениях и старайтесь устранить причины их возникновения при настройке того или иного датчика.

Список параметров фильтра Калмана:

- navModelNoise – дисперсия навигационной модели, которая предсказывает вертикальную и горизонтальные скорости, координаты в мировой системе координат.
- accVariance – дисперсия измерений аксселерометра (данный параметр пока не используется системой)
- baroAltVariance – дисперсия высоты, измеренной барометром
- lidarVelVariance1 – дисперсия вертикальной скорости, измеренной лидаром при удержании позиции (при горизонтальной скорости меньше 0,3 м/с)
- lidarVelVariance2 – дисперсия вертикальной скорости, измеренной лидаром во время движения дрона при горизонтальной скорости выше 0,3 м/с. Данный параметр следует настраивать только для полётов внутри зала, где нет изменений рельефа. Для полётов на открытом воздухе вертикальную скорость при помощи лидара во время движения дрона определить невозможно из-за изменения рельефа и растительности. Поэтому для полётов на открытом воздухе этот параметр лучше установить равным 1000000
- ofVelVariance1 – дисперсия горизонтальной скорости, измеренной оптическим датчиком смещения на высоте 0,3м
- ofVelVariance2 – дисперсия горизонтальной скорости, измеренной оптическим датчиком на высоте 0,9м. С увеличением высоты сигнал от оптического датчика смещения начинает сильнее шуметь!
- poseModelNoise – дисперсия модели, которая предсказывает крен, тангаж и курс
- yawRateVariance – дисперсия угловой скорости по курсу, измеренная гироскопом
- pitchRollRateVariance – дисперсия угловой скорости по крену и тангажу, измеренные гироскопом
- magHeadingVariance – дисперсия курса, измеренного магнетометром
- accPitchRollVariance – дисперсия крена и тангажа, измеренных акселерометром
- gpsHorSpeedVariance – множитель для параметра «gps.sAcc» для расчета точности горизонтальной скорости. Это измерение поступает в фильтр Калмана с дисперсией рассчитанной по формуле R=gpsHorSpeedVariance*gps.sAcc*gps.sAcc
- gpsVerSpeedVariance – множитель для параметра «gps.sAcc» для расчета точности вертикальной скорости. Это измерение поступает в фильтр Калмана с дисперсией рассчитанной по формуле R=gpsHorSpeedVariance*gps.sAcc*gps.sAcc
- gpsHorPosVariance – множитель для параметра «gps.hAcc» для расчета точности координат. Это измерение поступает в фильтр Калмана с дисперсией рассчитанной по формуле R=gpsHorPosVariance*gps.hAcc*gps.hAcc
- gpsVerPosVariance – множитель для параметра «gps.vAcc» для расчета точности высоты. Это измерение поступает в фильтр Калмана с дисперсией рассчитанной по формуле R=gpsVerPosVariance*gps.vAcc*gps.vAcc

# Обновление прошивки

Для обновления прошивки включите полётный контроллер и дождитесь когда он подключится к вашей WiFi-сети. Затем откройте браузер и введите адрес «ip-вашего контроллера/update», например, 192.168.1.33/update После этого должна загрузиться веб-страница для обновления прошивки. Сначала «Выберите файл» новой прошивки, а затем нажмите «Update Firmware»

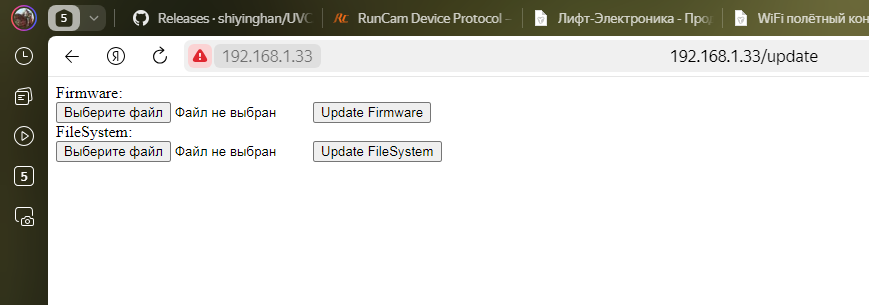
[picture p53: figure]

Текущую установленную версию прошивки можно узнать, открыв окно лога, в десктоп-приложении.

# Мобильное приложение

Прежде чем подключать вашу модель к мобильному приложению её нужно настроить через десктоп-приложение, как описано в главах выше, и сохранить настройки на флеш-память вашей модели. Если вы планируете подключать вашу модель к точке доступа, созданной вашим мобильным устройствам, то вам необходимо изменить параметры WiFi сети как это описано в главе 3. После того как вы установите успешное подключение с мобильным приложением, то откройте настройки и загрузите настройки по умолчанию из флеш-памяти вашей модели, нажав на кнопку «Load default». Затем сохраните эти настройки на диске вашего мобильного устройства, нажав на кнопку «Save». После сохранения обязательно проверьте, что настройки соответствуют действительности и нажмите на кнопку «Send».

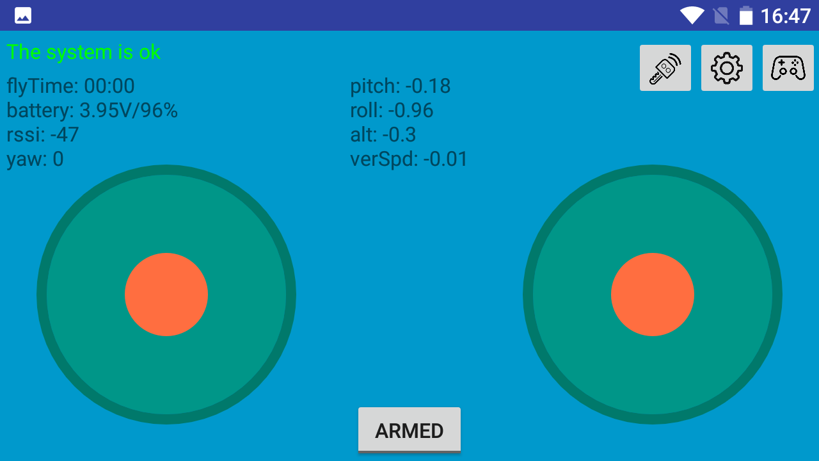
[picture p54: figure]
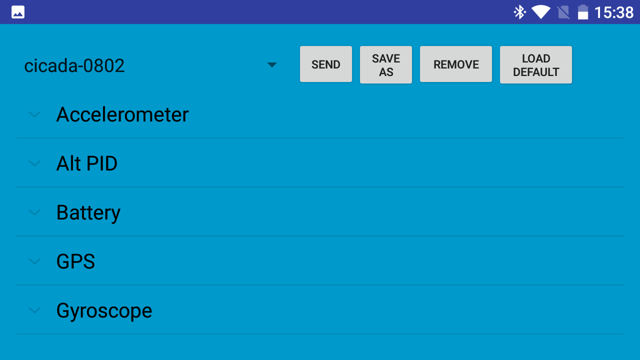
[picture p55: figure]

Управлять моделью из мобильного приложения можно при помощи виртуальных джойстиков, но лучше будет подключить к вашему мобильному устройству геймпад по блютуз каналу. После того как вы подключите геймпад, то его нужно настроить. Для этого откройте окно настройки геймпада и установите соответствующие клавиши для тех или иных команд.

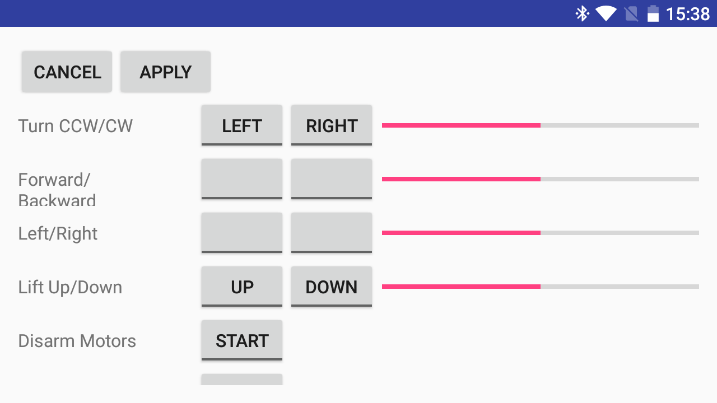
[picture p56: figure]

Мобильное приложение не поддерживает:

- настройку датчиков
- нет окна лога
- нет графиков телеметрии
- нет интерфейса для проверки двигателей

# Решение возможных технических проблем

Внимание: Качество стабилизации квадрокоптера в первую очередь и в большей степени зависит от качества работы его датчиков

Проблемы с акселерометром:

- Модель при взлете летит в сторону и практически не поддаётся управлению.
- При отпускании стиков модель постоянно летит в одну сторону.
- При отпускании стика управления высотой в режиме стабилизации вертикальной скорости модель начинает снижаться и не держит вертикальную скорость равную нулю. Также модель с трудом набирает высоту

Причиной описанных ваше проблем могут быть следующие факторы:

- Акселерометр плохо настроен. Попробуйте настроить его заново как описано в главе 6.
- Сильные вибрации от моторов - отбалансируйте пропеллеры, установите модуль IMU на двухсторонний скотч и припаяйте его к плате полетного контроллера тонкими проводами (софтмаунт).
- Сам акселерометр неисправный или плохого качества. Данную неисправность можно определить по графикам телеметрии. Для этого смотрите графики accel.rawX, accel.rawY, accel.rawZ Бракованные акселерометры и акселерометры плохого качества будут иметь для одной из осей сильные помехи.

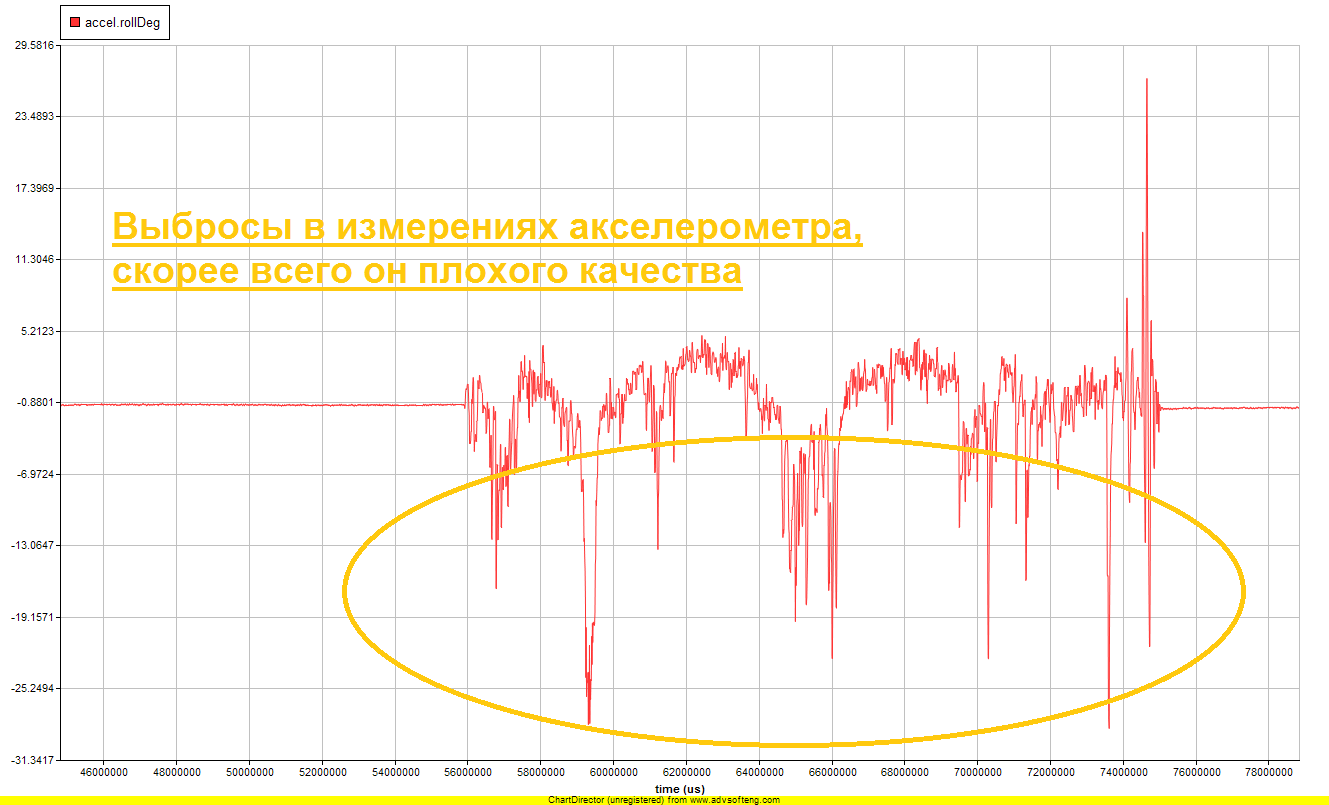
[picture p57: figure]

- Решить проблему с набором и удержанием высоты можно при помощи параметра «accUpOffset» в группе «Velocity-Z PID», если описанные выше методы не помогли. Если модель послу отпускания стика управления высотой в режиме стабилизации вертикальной скорости начинает снижаться, то увеличьте этот параметр на 0.1 и так далее пока модель более-менее не начнет удерживать вертикальную скорость равную нулю.

Проблемы с барометром:

- Модель неожиданно теряет высоту без команды как будто попадает в яму или, наоборот, резко без команды набирает высоту в режиме стабилизации вертикальной скорости.

Причиной описанной выше проблемы могут быть следующие факторы:

- Сильный ветер и другие атмосферные явления. Причем они будут оказывать влияние даже при полёте внутри помещения.
- Барометр установлен слишком близко к пропеллерам. Установите барометр дальше от пропеллеров или попробуйте установить барометр выше пропеллеров (над пропеллерами)
- Неисправный или плохого качества барометр

Проблемы с магнетометром:

- При наборе высоты или снижении модель меняет курс. Для решения этой проблемы установите магнетометр в другом месте вашей модели, на расстоянии минимум 50мм от проводом идущих к батарее и к моторам.

Проблемы с геймпадом:

- Геймпад не определяется десктоп-приложением. Для решения этой проблемы попробуйте отключить User Account Controller в Windows.

Полётный контроллер квадрокоптера Cicada, руководство пользователя 0

Компания «Лифт-Электроника» web: www.liftelectronica.ru, e-mail: liftelectronica@gmail.ru

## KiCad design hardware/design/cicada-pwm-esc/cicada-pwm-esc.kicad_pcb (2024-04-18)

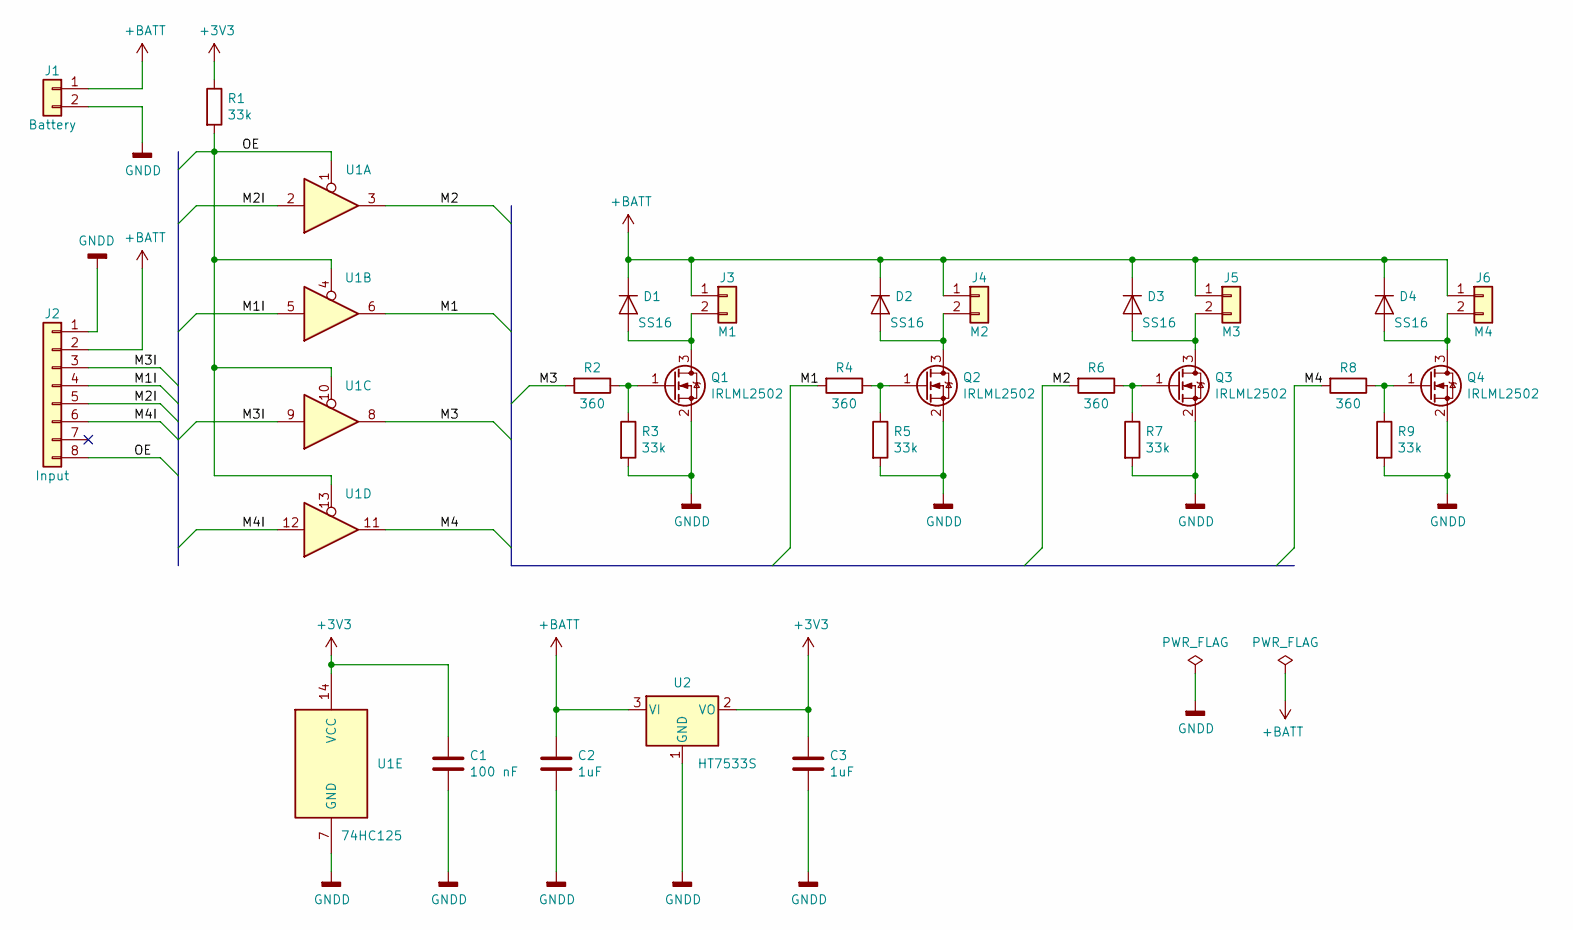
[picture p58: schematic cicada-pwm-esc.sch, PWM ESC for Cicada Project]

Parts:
C1: 100 nF; C_0805_2012Metric
C2, C3: 1uF; C_0805_2012Metric
D1, D2, D3, D4: SS16; D_SMA
J1: Battery; SolderWirePad_1x02_P5.08mm_Drill1.5mm
J2: Input; Molex_PicoBlade_53047-1610_1x08_P1.25mm_Vertical
J3: M1; Molex_PicoBlade_53047-0410_1x02_P1.25mm_Vertical
J4: M2; Molex_PicoBlade_53047-0410_1x02_P1.25mm_Vertical
J5: M3; Molex_PicoBlade_53047-0410_1x02_P1.25mm_Vertical
J6: M4; Molex_PicoBlade_53047-0410_1x02_P1.25mm_Vertical
Q1, Q2, Q3, Q4: IRLML2502; SOT-23
R1, R3, R5, R7, R9: 33k; R_0805_2012Metric
R2, R4, R6, R8: 360; R_0805_2012Metric
U1: 74HC125; SOIC-14_3.9x8.7mm_P1.27mm
U2: HT7533S; SOT-23

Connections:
+3V3: C1.1, C3.1, R1.1, U1.14 (VCC), U2.2 (VO)
+BATT: C2.1, D1.1 (K), D2.1 (K), D3.1 (K), D4.1 (K), J1.1, J2.2, J3.1, J4.1, J5.1, J6.1, U2.3 (VI)
/M1: R4.2, U1.6
/M1I: J2.4, U1.5
/M2: R6.2, U1.3
/M2I: J2.5, U1.2
/M3: R2.2, U1.8
/M3I: J2.3, U1.9
/M4: R8.2, U1.11
/M4I: J2.6, U1.12
/OE: J2.8, R1.2, U1.1, U1.4, U1.10, U1.13
GNDD: C1.2, C2.2, C3.2, J1.2, J2.1, Q1.2 (S), Q2.2 (S), Q3.2 (S), Q4.2 (S), R3.2, R5.2, R7.2, R9.2, U1.7 (GND), U2.1 (GND)
unnamed: D1.2 (A), J3.2, Q1.3 (D)
unnamed: D2.2 (A), J4.2, Q2.3 (D)
unnamed: D3.2 (A), J5.2, Q3.3 (D)
unnamed: D4.2 (A), J6.2, Q4.3 (D)
unnamed: Q1.1 (G), R2.1, R3.1
unnamed: Q2.1 (G), R4.1, R5.1
unnamed: Q3.1 (G), R6.1, R7.1
unnamed: Q4.1 (G), R8.1, R9.1

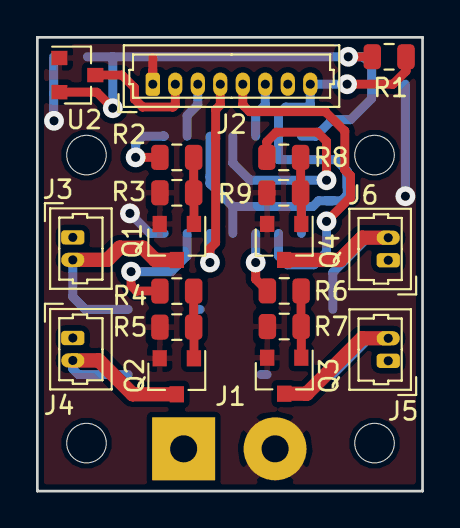
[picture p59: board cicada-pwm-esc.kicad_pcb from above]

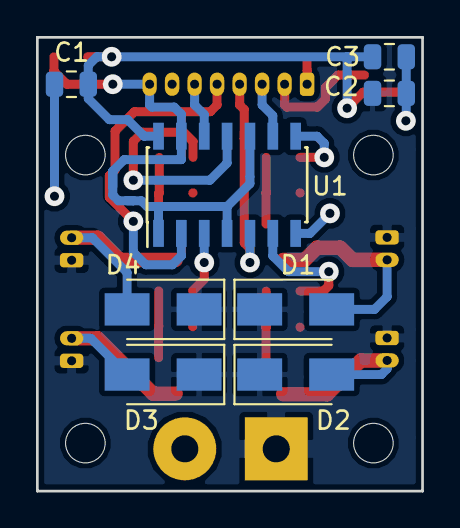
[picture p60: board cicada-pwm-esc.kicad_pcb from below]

Board: 2 copper layers, 21.4 x 25.2 mm, 28 parts (8 on the bottom side), 20 nets.

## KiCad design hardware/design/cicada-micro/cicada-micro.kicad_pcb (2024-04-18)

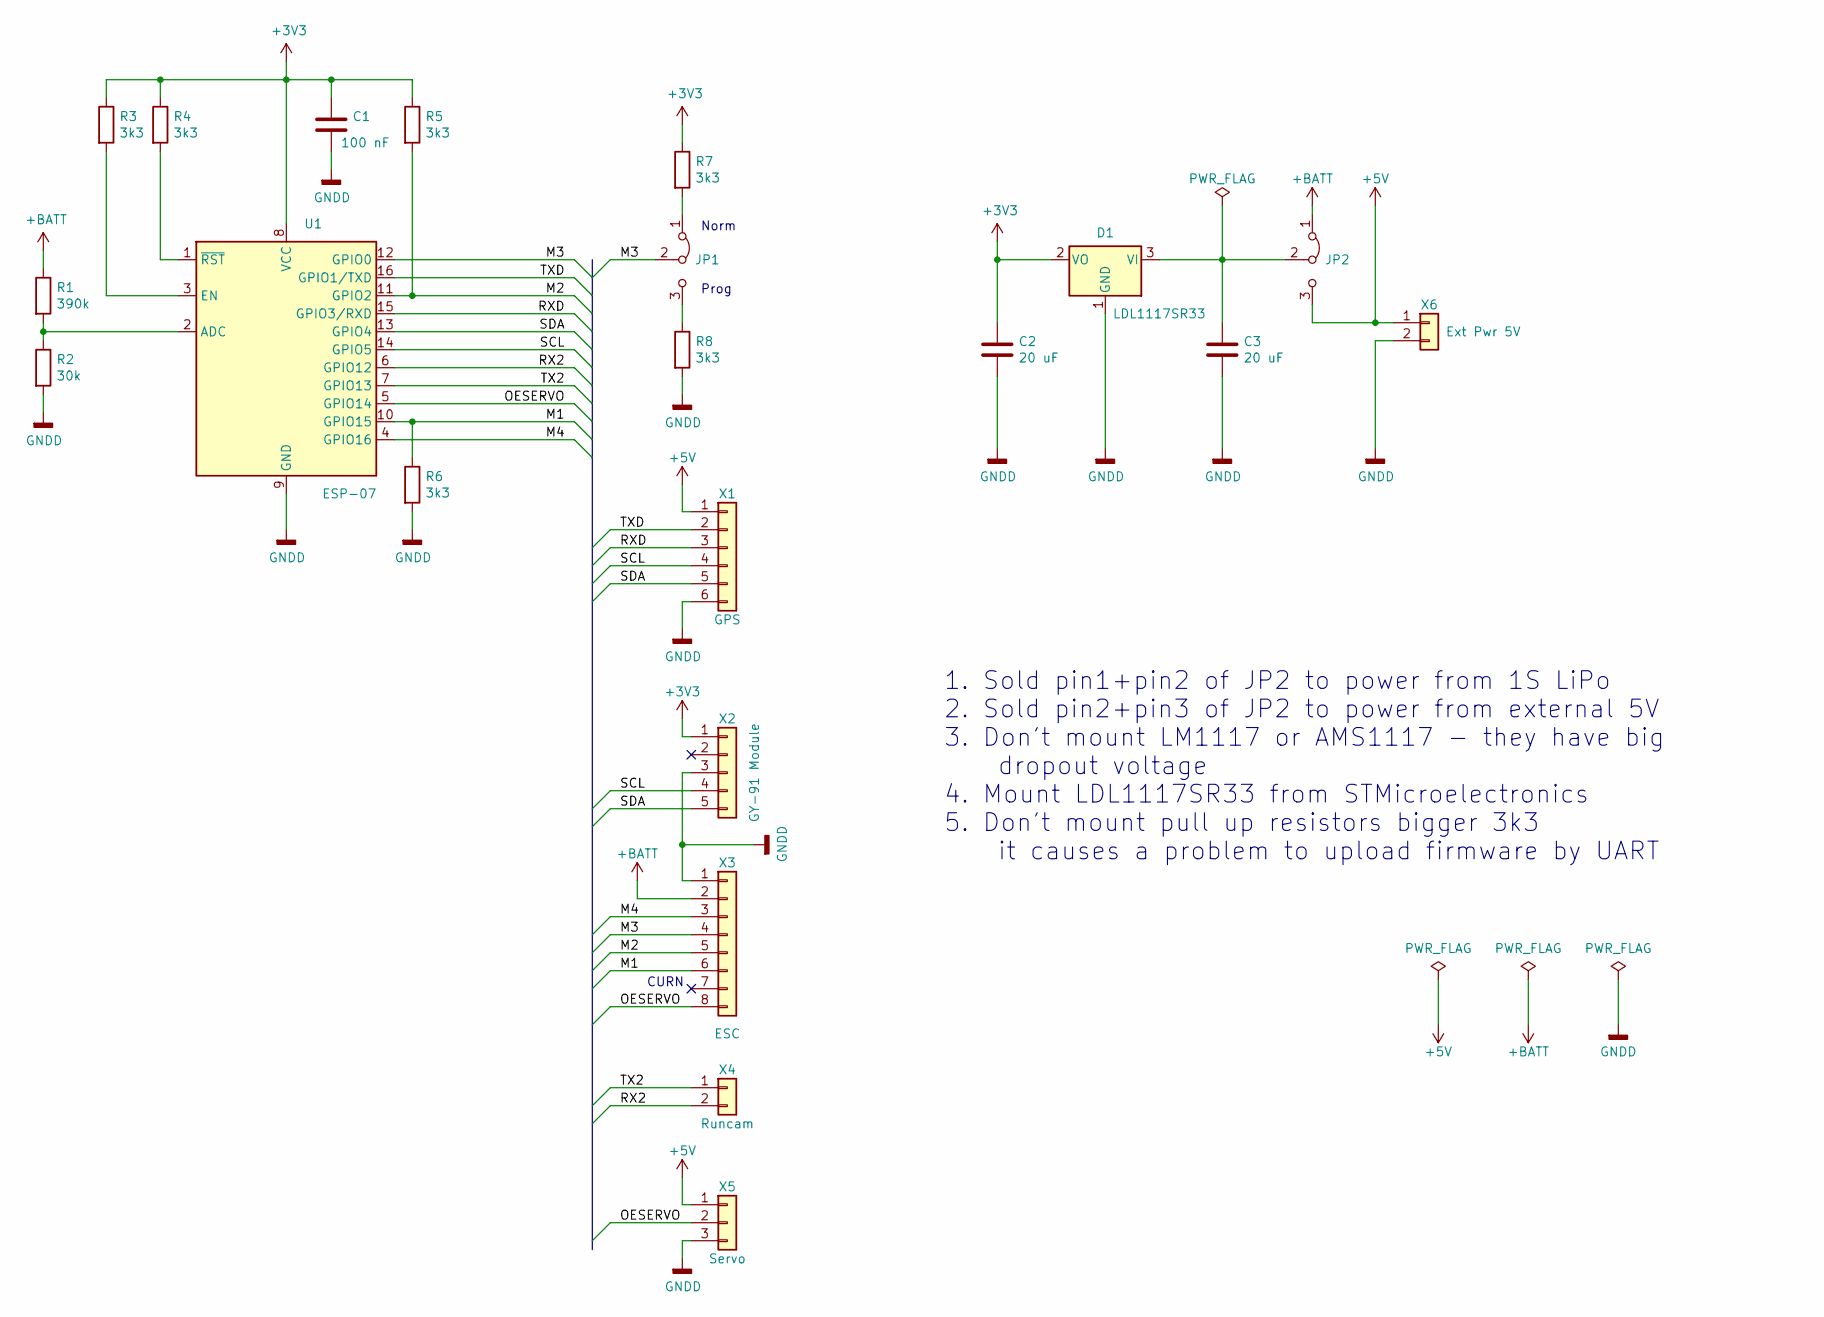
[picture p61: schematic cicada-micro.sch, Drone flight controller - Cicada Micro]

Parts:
C1: 100 nF; C_0805_2012Metric
C2, C3: 20 uF; C_1206_3216Metric
D1: LDL1117SR33; SOT-223-3_TabPin2
JP1, JP2: Jumper_3_Bridged12; SolderJumper-3_P1.3mm_Open_Pad1.0x1.5mm
R1: 390k; R_0805_2012Metric
R2: 30k; R_0805_2012Metric
R3, R4, R5, R6, R7, R8: 3k3; R_0805_2012Metric
U1: ESP-07; ESP-07-ThroughMount
X1: GPS; Molex_PicoBlade_53047-1210_1x06_P1.25mm_Vertical
X2: GY-91 Module; PinHeader_1x05_P2.54mm_Vertical
X3: ESC; Molex_PicoBlade_53047-1610_1x08_P1.25mm_Vertical
X4: Runcam; Molex_PicoBlade_53047-0410_1x02_P1.25mm_Vertical
X5: Servo; Molex_PicoBlade_53047-0610_1x03_P1.25mm_Vertical
X6: Ext Pwr 5V; Molex_PicoBlade_53047-0410_1x02_P1.25mm_Vertical

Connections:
+3V3: C1.1, C2.1, D1.2 (VO), R3.1, R4.1, R5.1, R7.1, U1.8 (VCC), X2.1
+5V: JP2.3 (B), X1.1, X5.1, X6.1; also elsewhere on the board
+BATT: JP2.1 (A), R1.1, X3.2; also elsewhere on the board
/M1: R6.1, U1.10 (GPIO15), X3.6
/M2: R5.2, U1.11 (GPIO2), X3.5
/M3: JP1.2 (C), U1.12 (GPIO0), X3.4
/M4: U1.4 (GPIO16), X3.3
/OESERVO: U1.5 (GPIO14), X3.8, X5.2
/RX2: U1.6 (GPIO12), X4.2
/RXD: U1.15 (GPIO3/RXD), X1.3
/SCL: U1.14 (GPIO5), X1.4, X2.4
/SDA: U1.13 (GPIO4), X1.5, X2.5
/TX2: U1.7 (GPIO13), X4.1
/TXD: U1.16 (GPIO1/TXD), X1.2
GNDD: C1.2, C2.2, C3.2, D1.1 (GND), R2.2, R6.2, R8.2, U1.9 (GND), X1.6, X2.3, X3.1, X5.3, X6.2
unnamed 15: C3.1, D1.3 (VI), JP2.2 (C); also elsewhere on the board
unnamed: JP1.1 (A), R7.2
unnamed: JP1.3 (B), R8.1
unnamed: R1.2, R2.1, U1.2 (ADC)
unnamed: R3.2, U1.3 (EN)
unnamed: R4.2, U1.1 (~RST)

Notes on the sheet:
Norm
Prog
CURN
1. Sold pin1+pin2 of JP2 to power from 1S LiPo 2. Sold pin2+pin3 of JP2 to power from external 5V 3. Don't mount LM1117 or AMS1117 - they have big dropout voltage 4. Mount LDL1117SR33 from STMicroelectronics 5. Don't mount pull up resistors bigger 3k3 it causes a problem to upload firmware by UART

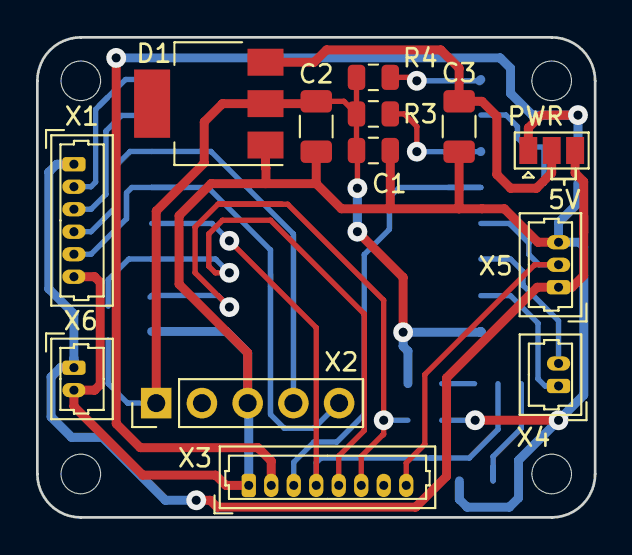
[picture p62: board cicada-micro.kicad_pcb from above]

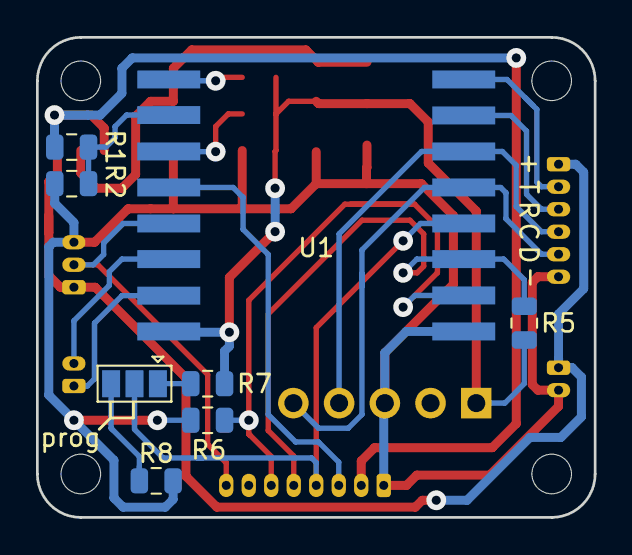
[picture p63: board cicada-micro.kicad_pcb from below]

Board: 2 copper layers, 31.0 x 26.7 mm, 21 parts (8 on the bottom side), 21 nets.

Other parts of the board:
PWR: Jumper_3_Bridged12; SolderJumper-3_P1.3mm_Open_Pad1.0x1.5mm

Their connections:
+5V: PWR.3; also elsewhere on the board
+BATT: PWR.1; also elsewhere on the board
unnamed 15: PWR.2; also elsewhere on the board

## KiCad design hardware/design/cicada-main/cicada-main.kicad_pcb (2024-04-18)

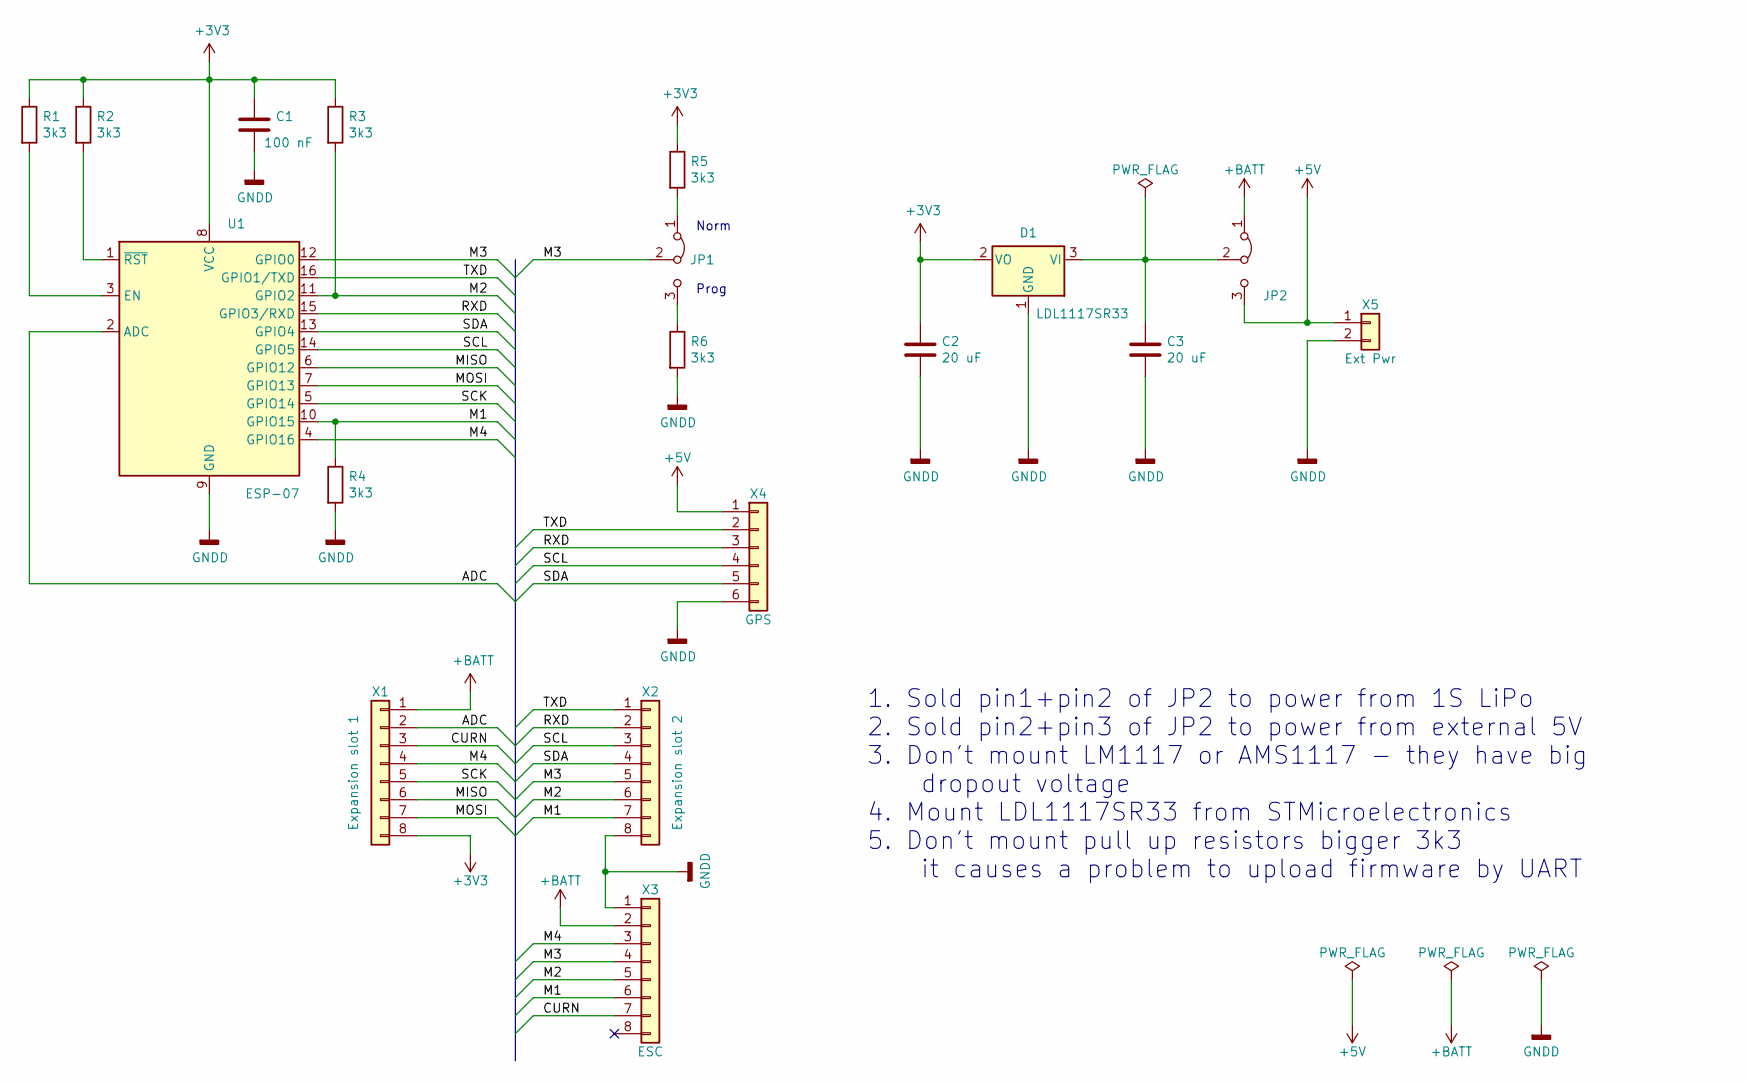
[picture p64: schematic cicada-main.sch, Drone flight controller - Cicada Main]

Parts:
C1: 100 nF; C_0805_2012Metric
C2, C3: 20 uF; C_1206_3216Metric
D1: LDL1117SR33; SOT-223-3_TabPin2
JP1, JP2: Jumper_3_Bridged12; SolderJumper-3_P1.3mm_Open_Pad1.0x1.5mm
R1, R2, R3, R4, R5, R6: 3k3; R_0805_2012Metric
U1: ESP-07; ESP-07-ThroughMount
X1: Expansion slot 1; PinHeader_1x08_P2.54mm_Vertical
X2: Expansion slot 2; PinHeader_1x08_P2.54mm_Vertical
X3: ESC; Molex_PicoBlade_53047-1610_1x08_P1.25mm_Vertical
X4: GPS; Molex_PicoBlade_53047-1210_1x06_P1.25mm_Vertical
X5: Ext Pwr; Molex_PicoBlade_53047-0410_1x02_P1.25mm_Vertical

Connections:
+3V3: C1.1, C2.1, D1.2 (VO), R1.1, R2.1, R3.1, R5.1, U1.8 (VCC), X1.8
+5V: JP2.3 (B), X4.1, X5.1
+BATT: JP2.1 (A), X1.1, X3.2
/ADC: U1.2 (ADC), X1.2
/CURN: X1.3, X3.7
/M1: R4.1, U1.10 (GPIO15), X2.7, X3.6
/M2: R3.2, U1.11 (GPIO2), X2.6, X3.5
/M3: JP1.2 (C), U1.12 (GPIO0), X2.5, X3.4
/M4: U1.4 (GPIO16), X1.4, X3.3
/MISO: U1.6 (GPIO12), X1.6
/MOSI: U1.7 (GPIO13), X1.7
/RXD: U1.15 (GPIO3/RXD), X2.2, X4.3
/SCK: U1.5 (GPIO14), X1.5
/SCL: U1.14 (GPIO5), X2.3, X4.4
/SDA: U1.13 (GPIO4), X2.4, X4.5
/TXD: U1.16 (GPIO1/TXD), X2.1, X4.2
GNDD: C1.2, C2.2, C3.2, D1.1 (GND), R4.2, R6.2, U1.9 (GND), X2.8, X3.1, X4.6, X5.2
unnamed: C3.1, D1.3 (VI), JP2.2 (C)
unnamed: JP1.1 (A), R5.2
unnamed: JP1.3 (B), R6.1
unnamed: R1.2, U1.3 (EN)
unnamed: R2.2, U1.1 (~RST)

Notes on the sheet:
Norm
Prog
1. Sold pin1+pin2 of JP2 to power from 1S LiPo 2. Sold pin2+pin3 of JP2 to power from external 5V 3. Don't mount LM1117 or AMS1117 - they have big dropout voltage 4. Mount LDL1117SR33 from STMicroelectronics 5. Don't mount pull up resistors bigger 3k3 it causes a problem to upload firmware by UART

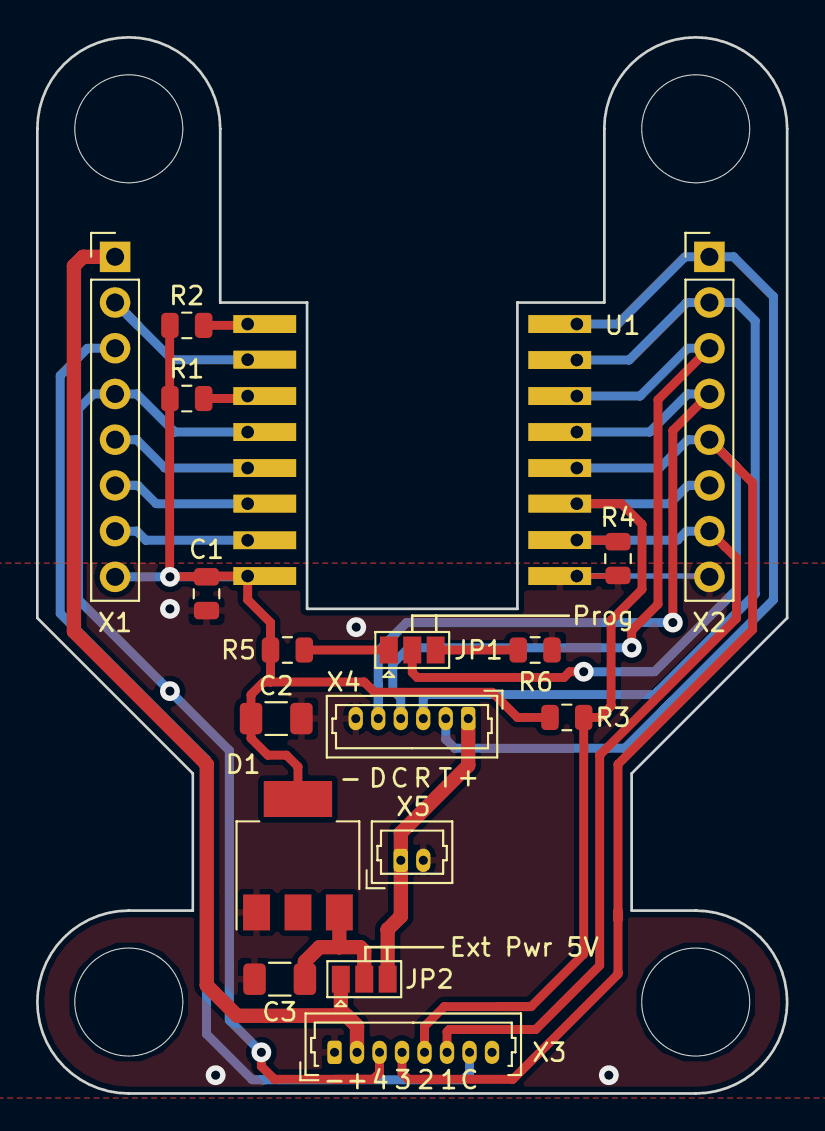
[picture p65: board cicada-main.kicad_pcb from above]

Board: 2 copper layers, 41.7 x 58.7 mm, 18 parts (0 on the bottom side), 22 nets.

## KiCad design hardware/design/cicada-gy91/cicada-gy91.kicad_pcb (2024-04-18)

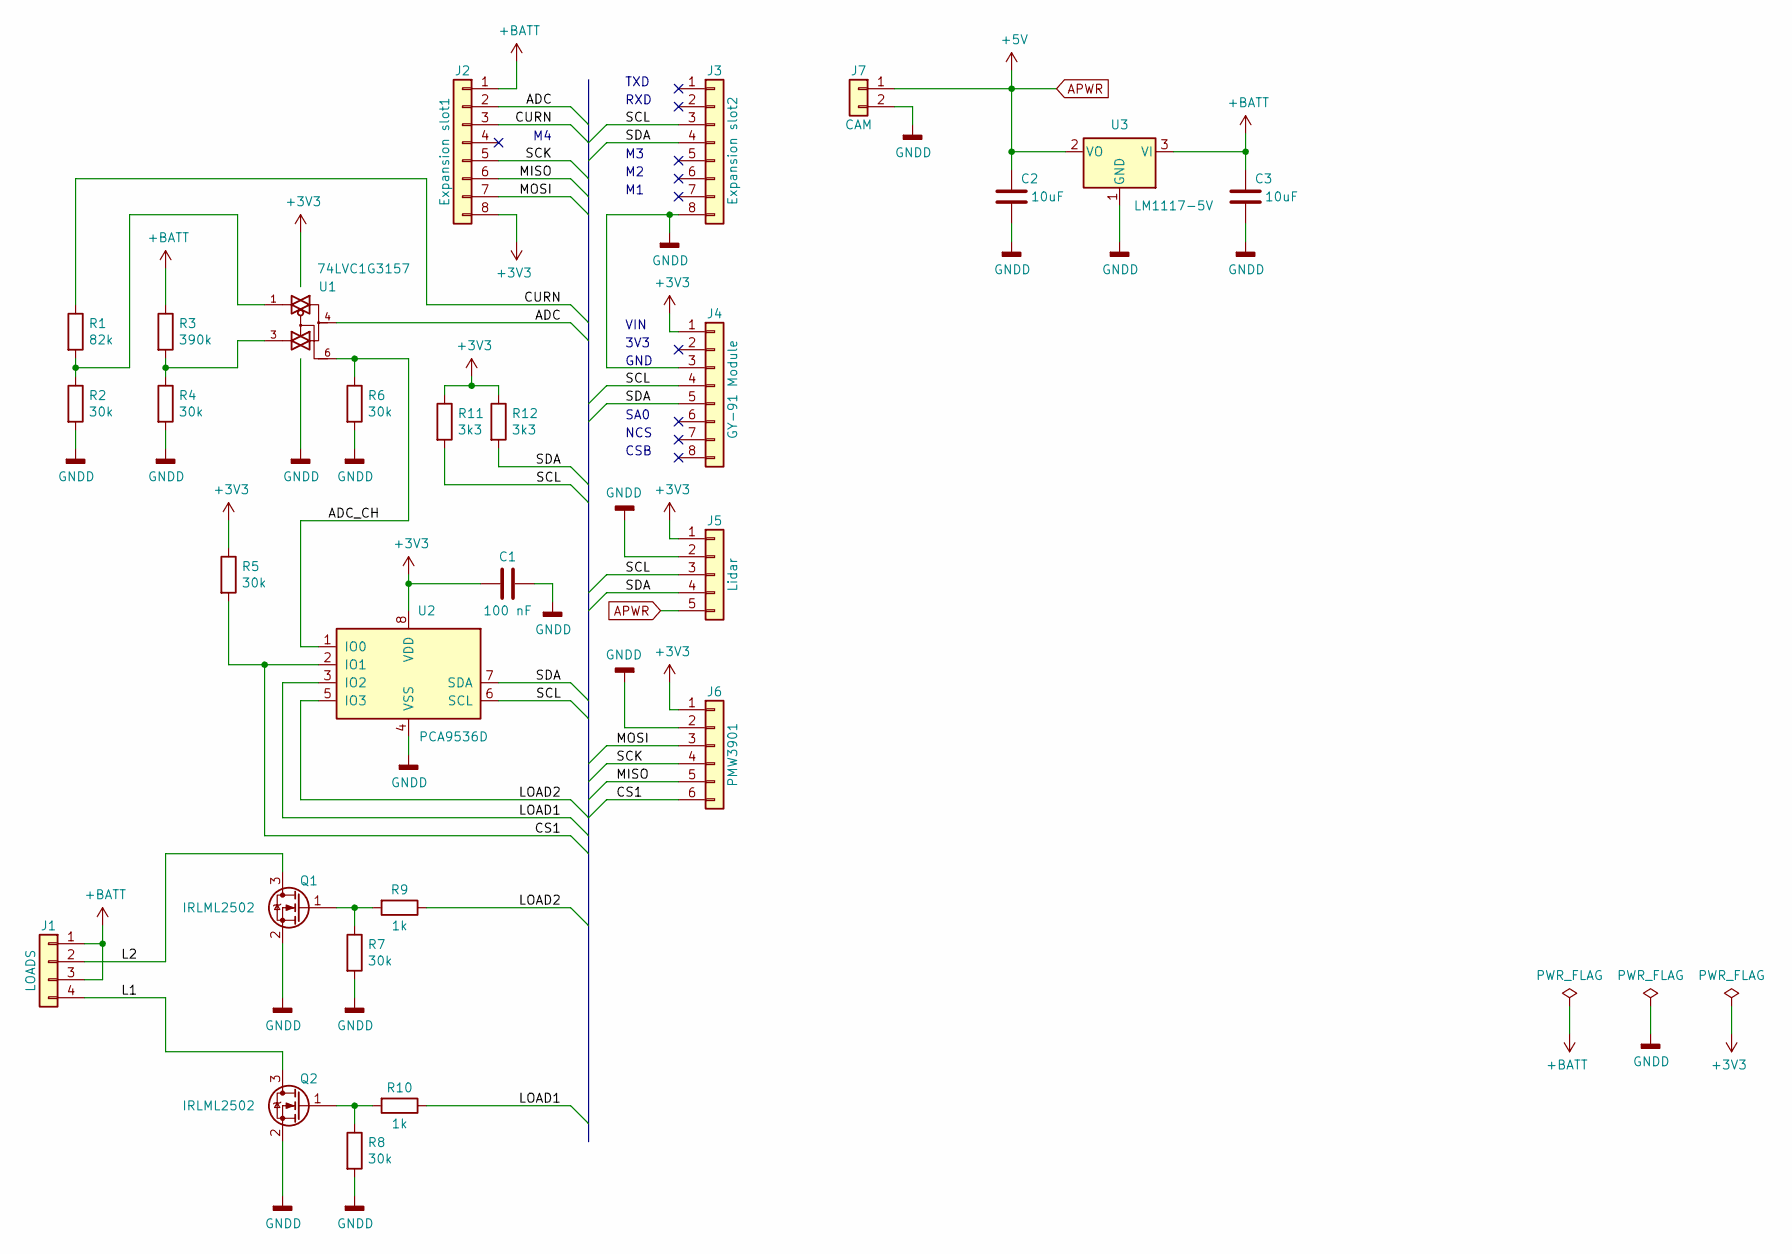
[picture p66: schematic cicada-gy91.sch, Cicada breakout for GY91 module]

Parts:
C1: 100 nF; C_0805_2012Metric
C2, C3: 10uF; C_0805_2012Metric
J1: LOADS; Molex_PicoBlade_53048-0810_1x04_P1.25mm_Horizontal
J2: Expansion slot1; PinSocket_1x08_P2.54mm_Vertical
J3: Expansion slot2; PinSocket_1x08_P2.54mm_Vertical
J4: GY-91 Module; PinHeader_1x08_P2.54mm_Vertical
J5: Lidar; Molex_PicoBlade_53048-1010_1x05_P1.25mm_Horizontal
J6: PMW3901; Molex_PicoBlade_53048-1210_1x06_P1.25mm_Horizontal
J7: CAM; Molex_PicoBlade_53048-0410_1x02_P1.25mm_Horizontal
Q1, Q2: IRLML2502; SOT-23
R1: 82k; R_0805_2012Metric
R2, R4, R5, R6, R7, R8: 30k; R_0805_2012Metric
R3: 390k; R_0805_2012Metric
R9, R10: 1k; R_0805_2012Metric
R11, R12: 3k3; R_0805_2012Metric
U1: 74LVC1G3157; SOT-363_SC-70-6
U2: PCA9536D; SOIC-8_3.9x4.9mm_P1.27mm
U3: LM1117-5V; SOT-223

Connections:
+3V3: C1.2, J2.8, J4.1, J5.1, J6.1, R5.1, R11.1, R12.1, U1.5 (VCC), U2.8 (VDD)
+BATT: C3.2, J1.1, J1.3, J2.1, R3.1, U3.3 (VI)
/ADC: J2.2, U1.4
/ADC_CH: R6.1, U1.6, U2.1 (IO0)
/CS1: J6.6, R5.2, U2.2 (IO1)
/CURN: J2.3, R1.1
/L1: J1.4, Q2.3 (D)
/L2: J1.2, Q1.3 (D)
/LOAD1: R10.1, U2.3 (IO2)
/LOAD2: R9.1, U2.5 (IO3)
/MISO: J2.6, J6.5
/MOSI: J2.7, J6.3
/SCK: J2.5, J6.4
/SCL: J3.3, J4.4, J5.3, R11.2, U2.6 (SCL)
/SDA: J3.4, J4.5, J5.4, R12.2, U2.7 (SDA)
APWR: C2.2, J5.5, J7.1, U3.2 (VO)
GND: C1.1, C2.1, C3.1, J3.8, J4.3, J5.2, J6.2, J7.2, Q1.2 (S), Q2.2 (S), R2.2, R4.2, R6.2, R7.2, R8.2, U1.2 (GND), U2.4 (VSS), U3.1 (GND)
unnamed: Q1.1 (G), R7.1, R9.2
unnamed: Q2.1 (G), R8.1, R10.2
unnamed: R1.2, R2.1, U1.1
unnamed: R3.2, R4.1, U1.3

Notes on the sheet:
NCS
CSB
3V3
VIN
GND
TXD
RXD
SA0

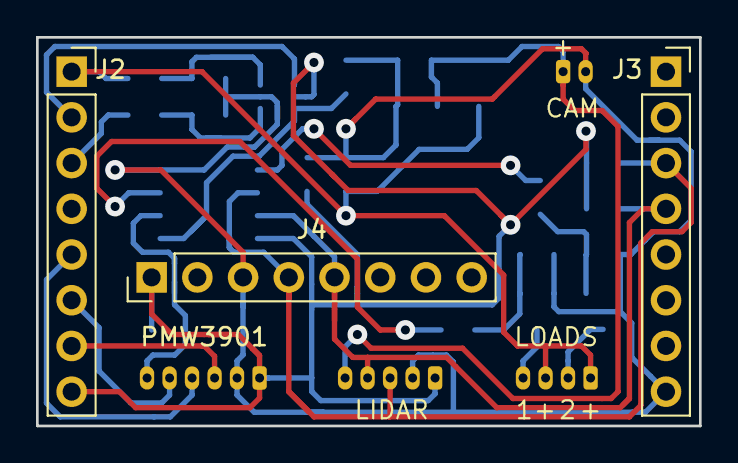
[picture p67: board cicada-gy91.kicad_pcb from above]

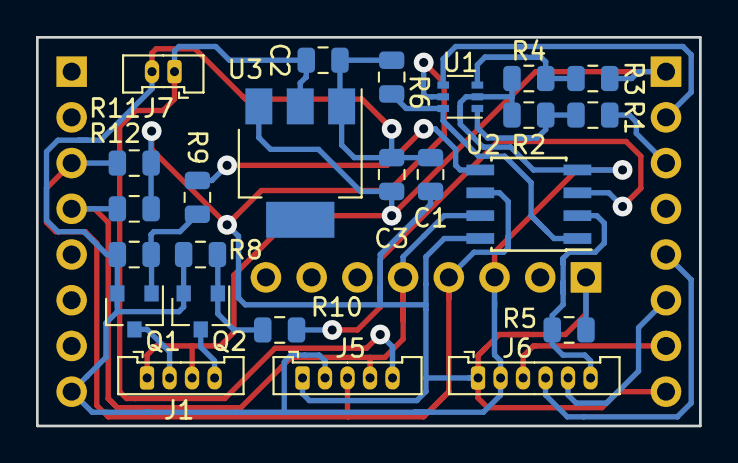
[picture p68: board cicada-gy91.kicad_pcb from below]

Board: 2 copper layers, 36.8 x 21.6 mm, 27 parts (24 on the bottom side), 21 nets.

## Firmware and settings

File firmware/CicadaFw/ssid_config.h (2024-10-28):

#ifndef SSID_CONFIG_H
#define SSID_CONFIG_H

#define DEFAULT_SSID_STR                          "cicada"
#define DEFAULT_PSK_STR                           "cosmos327"

#define DEFAULT_IP_ADDRESS_STR                    "192.168.43.243"
#define DEFAULT_GATEWAY_ADDRESS_STR               "192.168.43.1"
#define DEFAULT_SUBNET_STR                        "255.255.255.0"
#define DEFAULT_USE_DHCP_STR                      "n"

#define DEFAULT_WIFI_STA_MODE_STR                 "y"
// our param saving system supports only string literal
#define DEFAULT_WIFI_CHANNEL_STR                  "7"
#define DEFAULT_WIFI_TX_POWER_LEVEL_STR           "80"
#define DEFAULT_WIFI_PHY_MODE_STR                 "2"
#define DEFAULT_WIFI_RATE_STR                     "11"
#define DEFAULT_DRONE_ID_STR                      "0"

#endif

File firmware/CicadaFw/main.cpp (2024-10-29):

#include "pdl.h"
#include "main.h"

#include <ESP8266WiFi.h>
#include <Wire.h>
#include <FS.h>

//-----------------------------------------------------------------------------
// INSTALL
// 1. https://github.com/enjoyneering/ESP8266-I2C-Driver

//---------------------------------------------------------------
// VARIABLES

pdlDroneState droneState;

uint32_t pdlMicros()
{
  return micros();
}

//--------------------------------------------------------------
// INTERRUPTS

//--------------------------------------------------------------

/** Firmware version is not the same as PDL version.
 *  You can add for example supporting new sensor.
 *  This will be new firmware version and
 *  old desktop and mobile software will work with this version.
 *  But if you add new command or changed pdlDroneState
 *  this will be new PDL version. In this case old desktop and
 *  mobile software will not work with new firmware
 */
#define FW_VERSION "3"

void setup()
{
#ifdef SERIAL_DEBUG_ENABLED
  delay(5000);
#endif
  pdlResetLog();

  LOG_INFO("System started, fw v%s", FW_VERSION);

  Wire.begin();
  Wire.setClock(400000UL);  // In reality I observe 200 kHz by oscilloscope

  Serial.begin(115200);

  scanI2C();

#ifdef SERIAL_DEBUG_ENABLED
  pdlResetLog();  // scanI2C overflows log without expansion board
#endif

  pdlSetup(&droneState);

  LOG_INFO("System initialized. DroneState = %i bytes",sizeof(droneState));
}

void scanI2C()
{
  byte error, address;
  for(address = 1; address < 127; address++ )
  {
    // The i2c_scanner uses the return value of
    // the Write.endTransmisstion to see if
    // a device did acknowledge to the address.
    Wire.beginTransmission(address);
    error = Wire.endTransmission();

    if(error == 0)
    {
      LOG_INFO("I2Cdev=0x%x",address);
    }
    //else if(error==4) // this floods the log when no I2C devices
    //{
    //  LOG_ERROR("I2C error at address 0x%x",address);
    //}
  }
}

void pdlSaveDefaultCfg(pdlDroneState *ds)
{
  if(SPIFFS.begin() == false)
  {
    LOG_ERROR("Can't mount SPIFFS");
    return;
  }

  File file = SPIFFS.open("default.cfg","w+");
  if(!file)
  {
    LOG_ERROR("Can't open %s","default.cfg");
  }
  else
  {
    size_t written = file.write((unsigned char*)ds,sizeof(pdlDroneState));
    file.flush();

    if(written != sizeof(pdlDroneState))
    {
      LOG_ERROR("Can't save default.cfg");
    }
    else
    {
      LOG_INFO("New default.cfg has been saved");
    }
  }
  file.close();

  SPIFFS.end();
}

void pdlLoadDefaultCfg(pdlDroneState *ds)
{
  if(SPIFFS.begin() == false)
  {
    LOG_ERROR("Can't mount SPIFFS");
    return;
  }

  File file = SPIFFS.open("default.cfg","r");
  if(!file)
  {
    LOG_ERROR("Can't open %s","default.cfg");
  }
  else
  {
    size_t read = file.read((unsigned char*)ds,sizeof(pdlDroneState));

    if(read != sizeof(pdlDroneState))
    {
      LOG_ERROR("Can't load default.cfg");
    }
    else
    {
      LOG_INFO("default.cfg has been loaded");
    }

    if(ds->version != PDL_VERSION)
    {
      LOG_ERROR("invalid firmware version of default.cfg");
    }
  }
  file.close();

  SPIFFS.end();
}

uint8_t oldHostConnected = 0;

void loop()
{
  //-----------------------------------------
  #ifdef SERIAL_DEBUG_ENABLED
  if(pdlGetLogSize() > 0)
  {
    Serial.write(pdlGetLog(),pdlGetLogSize());
    pdlResetLog();
  }
  #endif
  //-----------------------------------------

  pdlUpdate(&droneState);

  if(!pdlIsHostConnected(&droneState))
  {
    pdlSafeStop(&droneState, 3.f);

    if(oldHostConnected)
    {
      LOG_INFO("Host is disconnected. Try to safe stop");
    }
  }

  oldHostConnected = pdlIsHostConnected(&droneState);
}

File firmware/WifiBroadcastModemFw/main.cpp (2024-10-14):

#include "WifiBroadcastModem.h"
#include <string.h>

#define LOG_BUF_SIZE  1024

char logBuf[LOG_BUF_SIZE];
int logPos = 0;

int log_printf(const char *format, ... )
{
  if(logPos >= LOG_BUF_SIZE)
    return 0;

  va_list args;
  va_start(args, format);
  int res = vsnprintf(&logBuf[logPos],LOG_BUF_SIZE - logPos,format,args);
  va_end(args);

  if(res > 0)
    logPos += res;

  if(logPos > LOG_BUF_SIZE)
    logPos = LOG_BUF_SIZE;

  return res;
}

char* getLog()
{
  return &logBuf[0];
}

int getLogSize()
{
  return logPos;
}

void resetLog()
{
  memset(&logBuf[0],0,LOG_BUF_SIZE);
  logPos = 0;
}

void setup()
{
  Serial.begin(921600);
  wbmSetup();
  log_printf("Started, fw.v1");
}

void loop()
{
  wbmUpdateSerial();

  if(getLogSize() > 0)
  {
    uint16_t written = wbmSendDataToHost((uint8_t*)getLog(),getLogSize(),1);
    if(written > 0)
    {
      resetLog();
    }
  }
}

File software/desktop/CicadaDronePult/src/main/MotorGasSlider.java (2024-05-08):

package main;

import java.awt.event.ActionEvent;
import java.awt.event.ActionListener;
import java.text.DecimalFormat;

import javax.swing.JLabel;
import javax.swing.JSlider;
import javax.swing.JTextField;
import javax.swing.event.ChangeEvent;
import javax.swing.event.ChangeListener;

import helper.NumericDocument;
import net.miginfocom.swing.MigLayout;
import pdl.DroneState;

public class MotorGasSlider extends javax.swing.JPanel
{
	private static final long serialVersionUID = -4207784842035696255L;
	
	public static final int DEFAULT_MIN_GAS = 0;
	public static final int DEFAULT_NULL_GAS = 0;
	public static final int DEFAULT_MAX_GAS = 1999;	// dshot switches motor off at value 2000!
	//public static final int MAX_GAS = 200;	// for PWM 25 kHz
	
	private JSlider mSlider;
	private JTextField mlbGas;
	private JLabel mlbGasPercent;
	private ChangeListener mcl;
	private boolean mValueAdjusting;
	private int mMinGas = DEFAULT_MIN_GAS;
	private int mNullGas = DEFAULT_NULL_GAS;
	private int mMaxGas = DEFAULT_MAX_GAS;
	
	private class OnGasChanged implements ChangeListener
	{
		@Override
		public synchronized void stateChanged(ChangeEvent e)
		{
			if(mSlider.getValueIsAdjusting())
				mValueAdjusting = true;
			
			int value = mSlider.getValue();
			float percent = value;
			
			if(value >= mNullGas)
			{
				percent /= mSlider.getMaximum();
				percent *= 100.0;
			}
			else
			{
				percent /= mSlider.getMinimum();
				percent *= 100.0;
			}
				
			DecimalFormat fmt = new DecimalFormat();
			fmt.setMaximumFractionDigits(0);
			fmt.setMinimumFractionDigits(0);
			
			mlbGas.setText(Integer.toString(value));
			mlbGasPercent.setText(fmt.format(percent) + "%");
			
			/*if(mSlider.getValueIsAdjusting() == false && mValueAdjusting == true)
			{
				if(mcl != null)
					mcl.stateChanged(e);
				
				mValueAdjusting = false;
			}*/
			if(mcl != null && mValueAdjusting)
				mcl.stateChanged(e);
			
			if(mSlider.getValueIsAdjusting() == false && mValueAdjusting == true)
				mValueAdjusting = false;
		}
	}
	
	private class OnGasSubmit implements ActionListener
	{
		@Override
		public void actionPerformed(ActionEvent e)
		{
			int gas = Integer.parseInt(mlbGas.getText());
			setGas(gas,true);
		}
	}
	
	public MotorGasSlider(String name)
	{
		mMinGas = DroneState.Motors.minGas;
		mNullGas = DroneState.Motors.nullGas;
		mMaxGas = DroneState.Motors.maxGas;
		
		this.createVertical(name);
	}
	
	public MotorGasSlider(String name, boolean horizontal)
	{
		mMinGas = DroneState.Motors.minGas;
		mNullGas = DroneState.Motors.nullGas;
		mMaxGas = DroneState.Motors.maxGas;
		
		if(horizontal)
			this.createHorizontal(name);
		else
			this.createVertical(name);
	}
	
	private void createVertical(String name)
	{
		this.setLayout(new MigLayout("insets 0 0 0 0","[35!, center]","[][grow][][]"));
		
		mSlider = new JSlider(JSlider.VERTICAL, mMinGas, mMaxGas, mNullGas);
		mlbGas = new JTextField();
		mlbGasPercent = new JLabel();
		
		mlbGas.setHorizontalAlignment(JTextField.CENTER);
		mlbGas.setDocument(new NumericDocument(0,false));
		mlbGas.addActionListener(new OnGasSubmit());
		
		mSlider.setMinorTickSpacing(1);
		mSlider.addChangeListener(new OnGasChanged());
		// To update labels set value
		mSlider.setValue(1);
		mSlider.setValue(0);
		
		this.add(new JLabel(name),"wrap");
		this.add(mSlider,"grow,wrap");
		this.add(mlbGas,"grow,wrap");
		this.add(mlbGasPercent);
	}
	
	private void createHorizontal(String name)
	{
		this.setLayout(new MigLayout("insets 0 0 0 0","[][grow][][]","[center]"));
		
		mSlider = new JSlider(JSlider.HORIZONTAL, mMinGas, mMaxGas, mNullGas);
		mlbGas = new JTextField();
		mlbGasPercent = new JLabel();
		
		mlbGas.setHorizontalAlignment(JLabel.CENTER);
		mlbGasPercent.setHorizontalAlignment(JLabel.CENTER);
		
		mSlider.setMinorTickSpacing(1);
		mSlider.addChangeListener(new OnGasChanged());
		// To update labels set value
		mSlider.setValue(1);
		mSlider.setValue(0);
		
		this.add(new JLabel(name));
		this.add(mSlider,"growx");
		this.add(mlbGas,"w 35!");
		this.add(mlbGasPercent,"w 30!");
	}
	
	public void addChangeListener(ChangeListener listener)
	{
		mcl = listener;
	}
	
	public void addGas(int gas)
	{
		gas += mSlider.getValue();
		this.setGas(gas, true);
	}
	
	public int getGas()
	{
		return mSlider.getValue();
	}
	
	public synchronized void setGas(int gas, boolean invokeListener)
	{
		if(!mValueAdjusting)
		{
			if(invokeListener)
				mSlider.setValueIsAdjusting(true);
			
			mSlider.setValue(gas);
			
			if(invokeListener)
				mSlider.setValueIsAdjusting(false);
		}
	}
	
	public void setMinMax(int min, int max)
	{
		mSlider.setMinimum(min);
		mSlider.setMaximum(max);
	}
}

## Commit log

2019-09-04 Первая версия с работающей электроникой и работающим управлением двигателями
    [copter.kicad_pcb, copter.sch, escaper.kicad_pcb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]
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2019-09-06 1. Перенес классы команд в пакет copter 2. Добавил класс для приёма телеметрических данных 3. Поправил пользовательский интерфейс диалога настроек 4. Отладил работу сообщений об авариях
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2019-09-10 1. Добавил в пульт класс слайдера для управления газом мотора 2. Добавил в прошивку чтение max17040 и отправку данных на хост 3. Сделал обработку данных от max17040 на стороне хоста
2019-09-11 1. Добавил в телеметрию RSSI, Accel, Gyro с отправкой и визуализацией на ПК 2. Перенес библиотеки для софта в папку проекта
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2019-09-14 Реализовал процесс калибровки датчиков, передачи калибровки в коптер, сохранение калибровки на стороне хоста
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2019-09-17 Уменьшил время опроса датчиков по I2C с 88 мс до 1-5 мс
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2019-09-27 Сделал всю инфраструктуру для ПИД: настройка, сохранение параметров, передача на коптер, визуализация и пр.
2019-09-28 Изменил сважность ШИМ двигателя с 256 до 1000 и переделал команду для передачи уровня газа
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2019-10-14 Много изменений, но главное необходимо выкинуть из схемы регистр 595 и управлять двигателями напрямую с ног МК. Тема для новой ветки
2019-10-16 Отладил работу PWM
    [copter.sch]
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2019-10-19 1. Перевёл проект прошивки в SloeberIDE 2. Переделал обновление прошивки на протокол HTTP 3. Изменил в протоколе формат данных для напряжения и процента батареи
2019-11-06 1. Сделал раму под TEENYPRO ESCAPER и двигатели 0703 2. Реализовал протокол DSHOT300 3. Различные эксперименты с PWM, высотой и др.
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2019-12-17 Переделал окно датчиков на Frame, добавил кнопку для сброса компаса, убрал кнопки для расчета калибровки акселерометра и гироскопа на хосте
2019-12-17 1. Вернулся к PWM 2. Сделал не симметричный ПИД, когда ПИД при изменении углов управляет только двигателями с одной стороны
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2020-04-16 Если в rtimulib включен компас, то отправляем его данные на хост, если нет, то считаем направление своим алгоритмом
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2020-04-25 1. Отладил алгоритм PDL. Теперь всё работает как было до этого 2. Обновил драйвер mpu6050 3. Исправил ошибку в драйвере mpu6050 в алгоритме калбировки акселерометра
    [main.cpp, rc.cpp]
2020-05-21 1. Добавил интерфейс для просмотра графиков 2. Поправил другие интерфейсы после перехода на PDL
2020-05-22 Сделал базовый класс для всех окон. Базовый класс умеет сохранять положение и размеры окна в файл настроек. Перенес интерфейс для управления моторами в отдельное окно. Добавил иконки для главных кноп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
2020-05-23 Перенес интерфейс состояния дрона в отдельное окно. Добавил механизм для получения текста или иконки из любой части приложения
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2021-01-06 Поправил изменение газа для каждого двигателя после того как был изменен общий раз
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2021-01-11 1. Сделал редактирование, сохранение и отправку настроек 2. В DroneState избавился от лишних классов для ПИД и гироскопа
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2021-01-15 1. Добавил в данные гироскопа поля для угловой скорости в радианах и градусах 2. Работа над багами в окне графиков
2021-01-29 Исправил баг, мешавший вводить отрицательное число в поле ввода
2021-02-22 1. Модифицировал прошивку под новую плату 2. Исправилял баги 3. Добился успешной работы ПИД для yaw
    [motor-tests.ods]
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2021-10-17 Сделал максимальный газ для двигателя 1999, так как при 2000 двигатели клинило. Добавил в ПИД ограничение на максимальное выходное значение
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2021-10-27 Добился более-менее хорошей стабилизации по оптическому датчику смещения, но код ещё грязный
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2021-11-08 Добавил в репозиторий проектные файлы "железа"
    [cicada-gy91.kicad_pcb, cicada-gy91.sch, cicada-main.kicad_pcb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]
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2021-11-09 Исправил YawPitchRoll, OpticalFlow X&Y, ПИДы в соответствии с принятой системой координат
    [RemoteControlGui.java]
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2021-11-09 Исправил калибровку трех-осевых датчиков, используя desktop приложение
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2024-04-18 added new board cicada-gy91-v3
    [cicada-gy91.kicad_pcb, cicada-gy91.sch]
2024-04-18 added new board cicada-main-v4
    [cicada-main.kicad_pcb, cicada-main.sch]
2024-04-18 added new board cicada-micro-v2
    [cicada-micro.kicad_pcb, cicada-micro.sch]
2024-04-18 added new board cicada-pwm-esc-v3
    [cicada-pwm-esc.kicad_pcb, cicada-pwm-esc.sch]
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2024-04-25 Added cicada-1404 drone
    [antenna-2G4Hz-3dbi.FCStd, antenna-5G8Hz-3dbi.FCStd, antenna-holder-2G4Hz-3dbi.FCStd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]
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2024-04-27 Added cicada-0802 quadcopter
    [bat-gnb-550-90c-1s.FCStd, camera-akk-ba3.FCStd, camera-ewrf7082ve.FCStd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]
2024-05-03 added imu-cup-for-mpu6050-and-bmp280 to cicada-0802 freecad project
    [cicada-0802.FCStd]
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2024-05-06 Added quadcopter cicada-1106
    [bat-gnb-850-2s-holder.FCStd, bn-180-holder.FCStd, cam-ewrf7082ve-holder.FCStd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]
2024-05-07 Added cicada-0816df drone
    [cicada-0816df.FCStd, motor-816-holder.FCStd, motor-coreless-816.FCStd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]
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2024-05-14 Updated prop-d102-protection, width changed from 3mm to 3.4mm
    [prop-d102-protection.FCStd]
2024-05-26 Fixed chapter 10. Input devices poll time is 40 ms (25Hz)
2024-05-26 Added fiberglass frame for cicada-0802
    [cicada-0802.FCStd]
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2024-05-30 Added CNC path to cut off protection legs from fiberglass
    [cicada-0802.FCStd]
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2024-05-30 Fixed memory leaks when load default command is received
    [baro.cpp, battery.cpp, imu.cpp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]
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2024-06-09 Added case for camera eachine tx06
    [case-for-eachine-tx06.FCStd]
2024-06-09 Added lighter case for camera akk ba3
    [case-for-akk-ba3-light.FCStd]
2024-06-09 Added holders for battery LiHv gnb-380
    [cicada-0802.FCStd]
2024-06-09 Fixed feature preventing flying away
    [main.cpp]
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2024-06-09 Fixed connecting to target and default wifi net
    [rc.cpp]
2024-06-25 Added a reversed cross-frame
    [esc.cpp]
2024-06-25 Added a description of a reversed cross-frame
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2024-08-13 Reinforced case-for-akk-ba3-light to be more stronger
    [case-for-akk-ba3-light.FCStd]
2024-09-06 Fixed switching to a trick mode in mobile app
2024-10-14 Added wifi broadcast mode
    [wifi-broadcast-modem.FCStd]
2024-10-17 Refactored the mechanism to avoid collisions in radio between two drones work at the same channel
    [WifiBroadcastModem.cpp, rc.cpp]
2024-10-21 working around the problem: we can't connect to softAp from some smarthphones and PCs
    [rc.cpp]
2024-10-21 Fixed: the system resets when we try to switch back to wifi normal mode
    [rc.cpp]
2024-10-22 Added the serial port driver for Android application and bug fixing
    [RemoteControlGui.java, rc.cpp]
2024-10-28 Bug fixing around WifiBroadcast mode
    [RemoteControlGui.java, rc.cpp]
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2024-10-30 Fixed: runcam is not found
    [camera.cpp]
2024-11-11 Added new drone cicada-0802-star
    [bat-gnb-lihv-380-60c-1s.FCStd, camera-eachine-tx06.FCStd, case-for-akk-ba3-strong.FCStd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]
2024-12-24 Reinforced the case for eachine tx06 camera
    [case-for-eachine-tx06.FCStd, cicada-0802-star.FCStd]
